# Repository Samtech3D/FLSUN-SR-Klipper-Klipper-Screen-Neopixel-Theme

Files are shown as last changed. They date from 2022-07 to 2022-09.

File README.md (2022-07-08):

If you like my Work Buy Me a Coffee! 🌹❤😍💙

Download (https://www.paypal.me/samiartmedia)

**This repository contains settings for Klipper, KlipperScreen and Neopixel for FLSUN Super Racer with necessary scripts and macros using MKS Robin Nano V3.0 motherboard.**<br /><br />

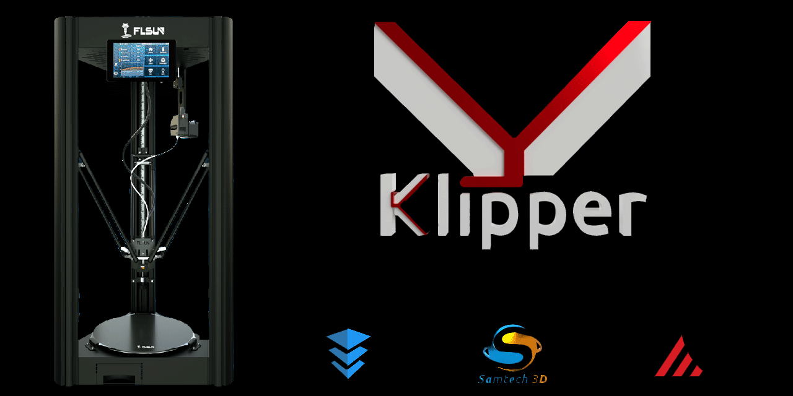
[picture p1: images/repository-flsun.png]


## References
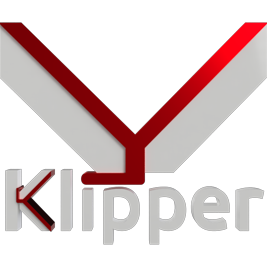
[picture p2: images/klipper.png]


- https://www.klipper3d.org/
- https://github.com/th33xitus/kiauh
- https://github.com/jordanruthe/KlipperScreen
- https://www.klipper3d.org/Pressure_Advance.html
- https://www.klipper3d.org/Resonance_Compensation.html
- https://www.klipper3d.org/Measuring_Resonances.html
- https://github.com/digitalninja-ro/klipper-neopixel

## Hardware
- The recommended hardware is a Raspberry Pi 2, Raspberry Pi 3, or Raspberry Pi 4 https://www.klipper3d.org/FAQ.html
- This installation is based on MKS Robin Nano V3.0 with TMC2209 stepper drivers and Raspberry Pi4 Touchscreen Display  "Work in Progress for other motheroards."
- Raspberry Pi 4 Touchscreen Display https://klipperscreen.readthedocs.io/en/latest/Hardware/
- ADXL 345 for input shaper test (optional) https://www.klipper3d.org/Measuring_Resonances.html

## Installation
- Prepare your OS image (I'm using Raspberry Pi OS Legacy (Buster version) to use omx-player to run my splash screen on startup). https://www.raspberrypi.com/software/ , or you can use Raspberry PI Imager
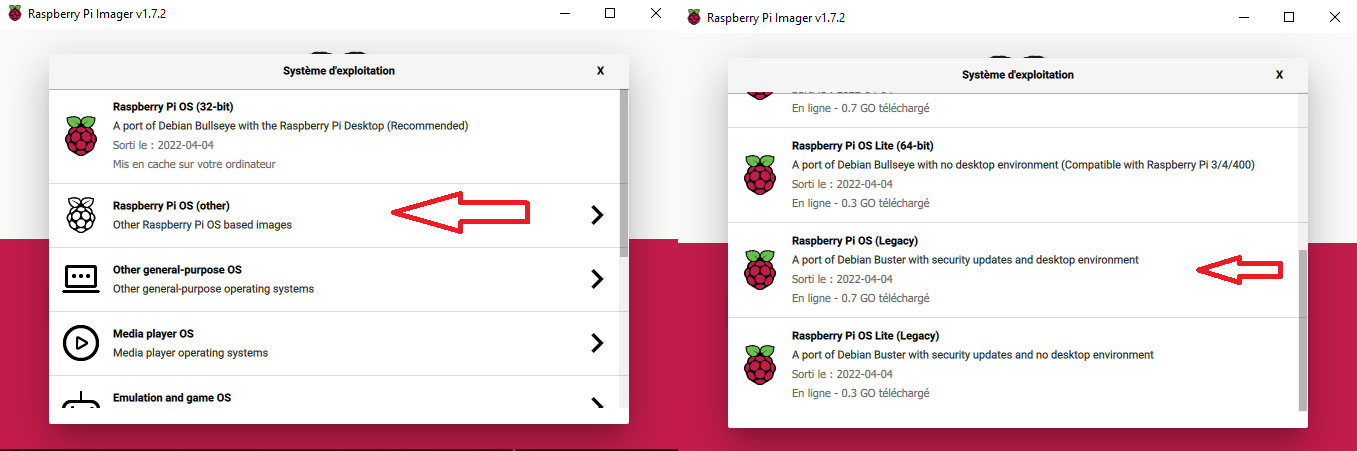
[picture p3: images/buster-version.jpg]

 
- Find the Raspberry Pi IP (you can use fing app on your phone).
- Easy way to install Klipper with Kiauh: https://github.com/th33xitus/kiauh
    - You need to install git first, on SSH run this command: `sudo apt-get install git -y`.
    - After git is installed, use the following commands in the given order to download and execute the script:

```
cd ~

git clone https://github.com/th33xitus/kiauh.git

./kiauh/kiauh.sh
```
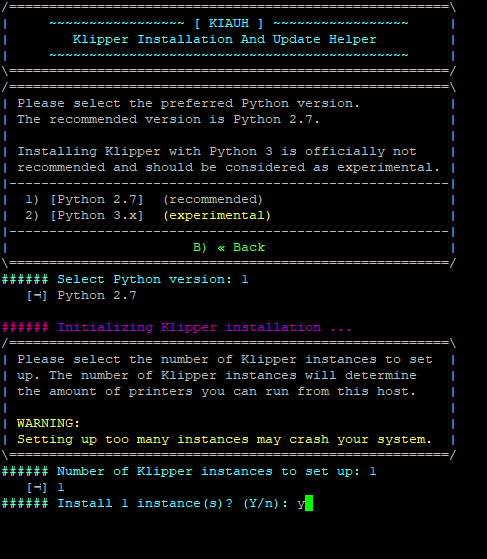
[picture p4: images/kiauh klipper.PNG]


### Install with Kiauh script in the following order:
  #### 1.Klipper
  #### 2.Moonraker
  #### 3.Fluidd or Mainsail or both using a different port for the 2nd install, example: Port 81 (I added themes for Mainsail)
  #### 4.KlipperScreen

- On your browser type your Raspberry Pi IP to open Fluidd interface then import:
    - .theme (folder)
    - printer.cfg
    - klipperScreen.conf
    - macros.cfg
    - led_progress.cfg (if you have neopixel installed) 
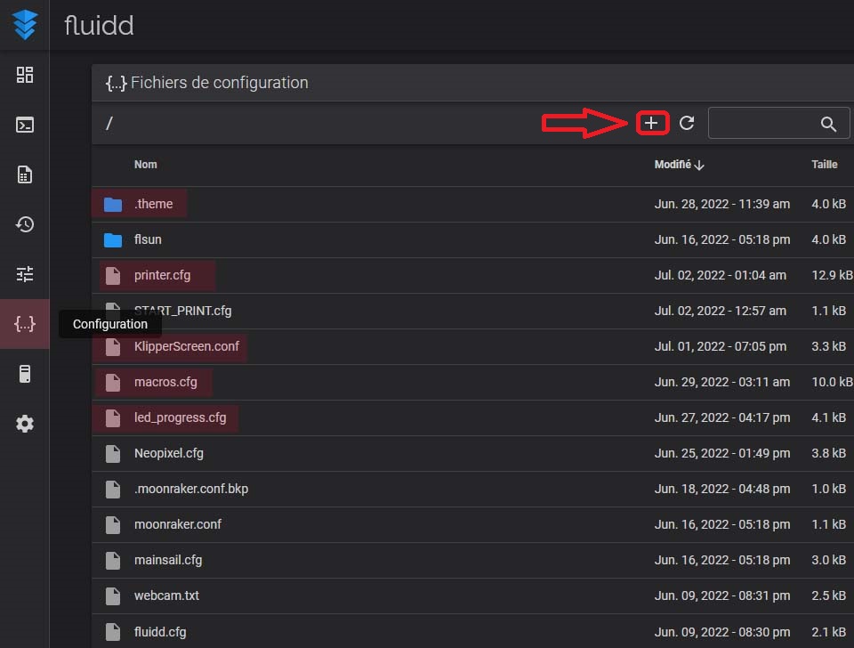
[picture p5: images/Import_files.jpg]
   

### Build firmware and flash your motherboard
- Open SSH to compile the microcontroller code, start by running these commands: 

```
cd ~/klipper/
make menuconfig
```

### [*] Enable extra low-level configuration options
### Microcontroller Architecture (STMicroelectronics STM32)  --->
  ### STMicroelectronics STM32
  ### Processor model (STM32F407)  --->
  ### Bootloader offset (48 KiB bootloader (MKS Robin Nano V3))  --->
  ### Clock Reference (8 MHz crystal)  ---> 
  ### Communication interface (USB (on PA11/PA12))  --->

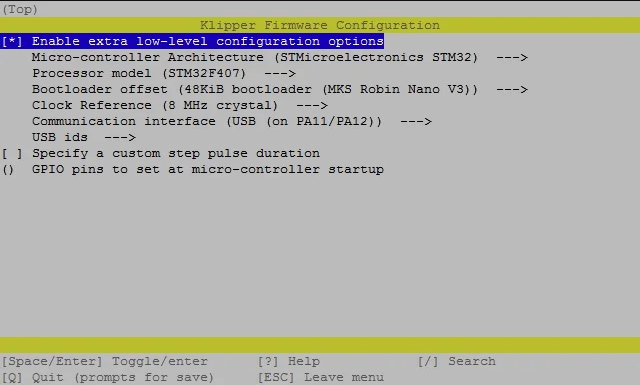
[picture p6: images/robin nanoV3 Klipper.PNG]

- Press "Q" to exit, and then "Y" to save and run make command to flashing image for your printer motherboard.

```
make
```

If you have a problem to flash your firmware enter this command:

```
make clean
git pull
make
```

- Open WinSCP App (https://winscp.net/eng/download.php), connect with your Raspberry Pi IP and navigate to:
- /home/pi/klipper/out
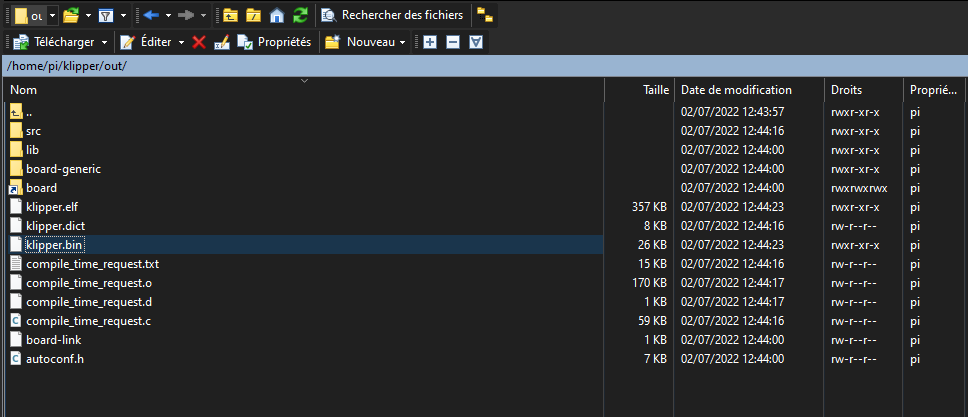
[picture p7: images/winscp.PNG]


  - Copy and paste "klipper.bin" firmware to your desktop and rename the file to "Robin_nano_v3.bin".
  - Format your microSD card (be careful, do not use the one present in the Raspberry Pi) in FAT32 with allocation unit size 4096 (max capacity 32GB) then paste "Robin_nano_v3.bin" file in the root of your  microSD card.
  - With printer off, insert the microSD card into the dedicated port on the motherboard and turn on the printer.
  - Flash procedure starts (without displaying anything on the screen) and lasts a few seconds.
  - Connect your Raspberry Pi to your printer using USB cable.
  - Comeback to your SSH session then type:

```
ls /dev/serial/by-id/*
```

It should report something similar to the following:

```
/dev/serial/by-id/usb-Klipper_stm32f407xx_4D0052000950325436303720-if00
```
   - Each printer have a unique serial
   - Copy your serial then paste it in printer.cfg


```
[mcu]
serial: /dev/serial/by-id/usb-Klipper_stm32f407xx_4D0052000950325436303720-if00#Configuration of the primary micro-controller Use ls /dev/serial/by-id/*
baud: 250000
restart_method: command
```

- If everything is correct, you can connect your Raspberry Pi with your printer.

### Calibration

## 1 - Z-Offset "You can do this with Fluidd, Mainsaill terminal or via KlipperScreen"
   - Home 
   - Make sure to connect bed level probe before to start the following command.
   - On your terminal run `PROBE_CALIBRATE` command. Printer will probe 5 times then stop at 20 mm of the bed.
   - Remove bed level probe.
   - Paper test: This involves placing a piece of plain paper between the bed and the nozzle so that the sheet of paper slightly scrapes the nozzle.
   - Use the TESTZ command to request the nozzle to move closer to the paper. For example, `TESTZ z=-1` to go down, `TESTZ z=1` to go up. It's also possible to use `TESTZ Z=+` or `TESTZ Z=-` to "bisect" the last position that is to move to a position halfway between two positions.
   - When you got the right Z-Offset, run `ACCEPT` then `SAVE_CONFIG` commands or `ABORT` command to stop the calibration procedure.
## 2 - DELTA_CALIBRATE  
  - Home.
  - Make sure to connect bed level probe before to start the following command.
  - Run `DELTA_CALIBRATE` command and wait until finish then `SAVE_CONFIG`.
## 3 - BED_MESH_CALIBRATE
  - Home
  - Make sure to connect bed level probe before to start the following command.
  - Run `BED_MESH_CALIBRATE` command and wait until finish then `SAVE_CONFIG`.
## 4 - Print 1st layer test using "1st_layer_test0.2.gcode" [ Download ] 
  - Adjust your Z-Offset while printing.
  - When it's done, run `Z_OFFSET_APPLY_PROBE` then `SAVE_CONFIG` commands to save the new Z-Offset.
  - If you still have problem with your Z-Offset, after G28 line add your Z-Offset value to your Start-Gcode, Ex:`SET_GCODE_OFFSET Z=0.35`.
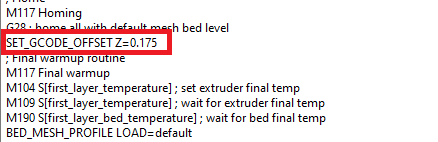
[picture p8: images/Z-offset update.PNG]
    

### Install Samtech3d Themes For Klipper Screen
  - Navigate to `/home/pi/KlipperScreen/styles` using WinSCP App then drag and drop "Samtech-red & Samtech-blue" folders.
  - In KlipperScreen Go to Configuration / Settings and scroll down to Icon Theme "Samtech-red & Samtech-blue".

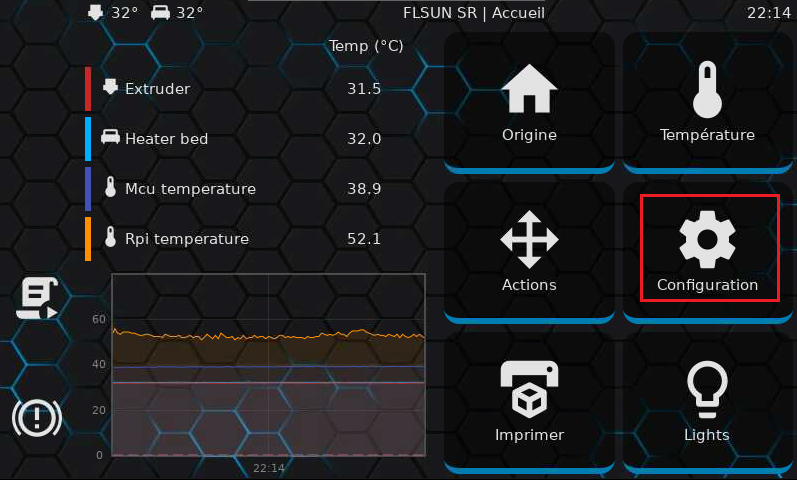
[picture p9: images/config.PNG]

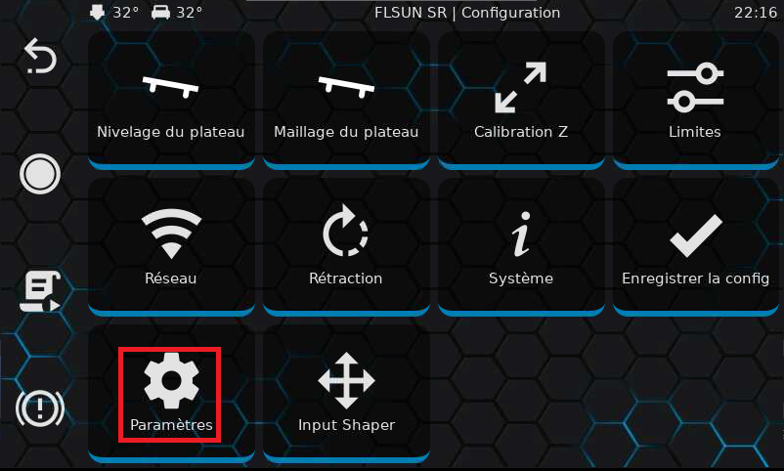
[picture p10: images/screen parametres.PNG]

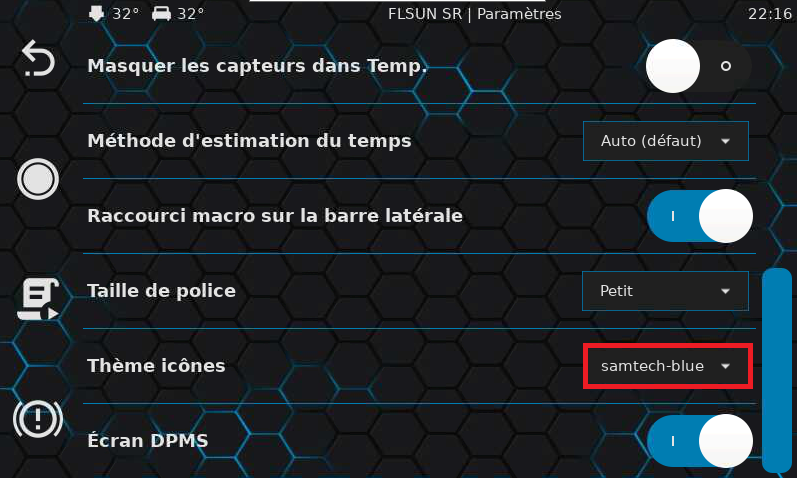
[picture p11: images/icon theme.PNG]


### Neopixel Installation

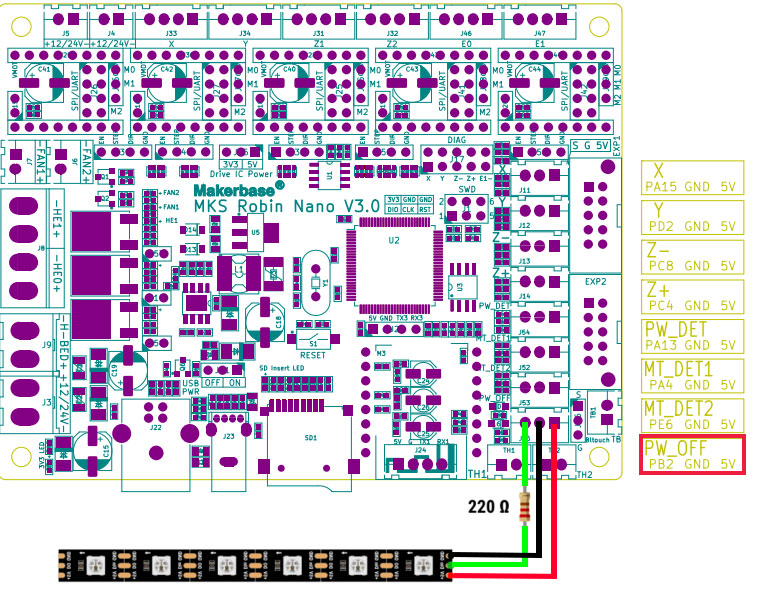
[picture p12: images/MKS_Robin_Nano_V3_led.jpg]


Or 

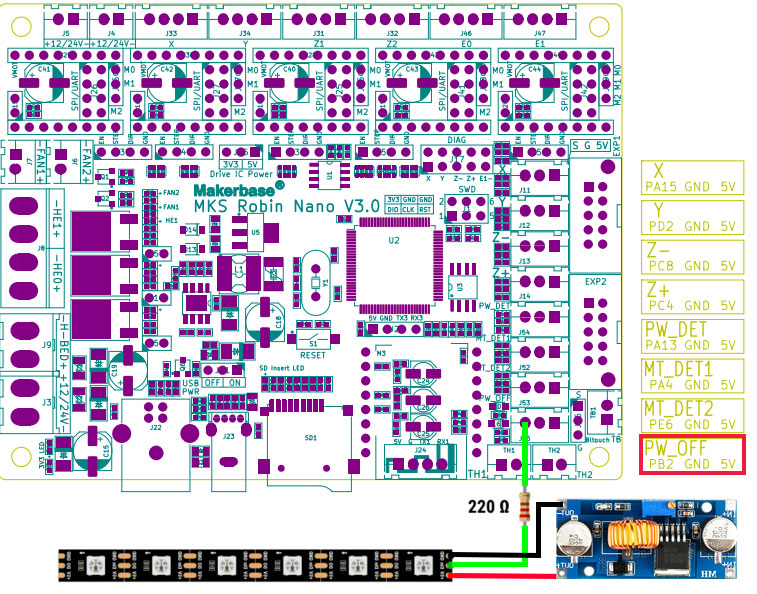
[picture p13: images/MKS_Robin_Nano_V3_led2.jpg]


  - Add `led_progress.cfg` then included in your printer.cfg `[include led_progress.cfg]`

  - Add this lines to your printer.cfg

  ```
  [neopixel neo]
  pin: PB2
  chain_count:15
  color_order: GRB
  initial_RED: 0.0
  initial_GREEN: 0.0
  initial_BLUE: 0.0
  initial_WHITE: 0.0

  ```
  - Add this lines to your KlipperScreen.conf

  ```
#####################################################
########## My Klipper Screen Neopixel  ##############
#####################################################

[menu __main Lights] #Lights
name: Lights
icon: light

[menu __main Lights Lights_On]
name: Lights On
icon: light
method: printer.gcode.script
params: {"script":"neopixel_on"}
[menu __main Lights Lights_Off]
name: Lights Off
icon: light
method: printer.gcode.script
params: {"script":"neopixel_off"}
[menu __main Lights blue]
name: blue
icon: lightB
method: printer.gcode.script
params: {"script":"blue_on"}

[menu __main Lights red]
name: red
icon: lightR
method: printer.gcode.script
params: {"script":"red_on"}
[menu __main Lights green]
name: green
icon: lightG
method: printer.gcode.script
params: {"script":"green_on"}     

[menu __main Lights extruder_temp]
name: Glow
icon: extruder
method: printer.gcode.script
params: {"script":"extrudertemp"}  
[menu __main Lights extruder_progress]
name: Progression
icon: extruder
method: printer.gcode.script
params: {"script":"extruderprogress"}  

[menu __main Lights bedtemp]
name: Glow
icon: bed
method: printer.gcode.script
params: {"script":"bedtemp"}  
[menu __main Lights bedprogress]
name: Progression
icon: bed
method: printer.gcode.script
params: {"script":"bedprogress"}  
[menu __main Lights percentprogress]
name: Progression
icon: percentage
method: printer.gcode.script
params: {"script":"percentprogress"}  
[menu __main Lights percentglow]
name: Glow
icon: percentage
method: printer.gcode.script
params: {"script":"percentglow"}  
[menu __main Lights speedprogress]
name: Progression
icon: speed+
method: printer.gcode.script
params: {"script":"speedprogress"} 
```
 - Add this lines to your macros.cfg

 ```
#############################################
######### NeoPixel By Samtech 3D#############
#############################################
[gcode_macro neopixel_on]
gcode:
          SET_LED LED=neo RED=1 GREEN=1 BLUE=1
[gcode_macro neopixel_off]
gcode:
          NEOPIXEL_DISPLAY LED="neo" TYPE=clear
          
[gcode_macro blue_on]
gcode:
          SET_LED LED=neo RED=0 GREEN=0 BLUE=1
[gcode_macro red_on]
gcode:
          SET_LED LED=neo RED=1 GREEN=0 BLUE=0   
[gcode_macro green_on]
gcode:
          SET_LED LED=neo RED=00 GREEN=1 BLUE=0  
[gcode_macro extrudertemp]
gcode:
          neopixel_display LED=neo TYPE=extruder_temp MODE=glow
[gcode_macro extruderprogress]
gcode:
          neopixel_display LED=neo TYPE=extruder_temp MODE=progress     

[gcode_macro bedtemp]
gcode:
          neopixel_display LED=neo TYPE=bed_temp MODE=glow  
[gcode_macro bedprogress]
gcode:
          neopixel_display LED=neo TYPE=bed_temp MODE=progress          
[gcode_macro percentprogress]
gcode:
          neopixel_display LED=neo TYPE=print_percent  MODE=progress        
[gcode_macro percentglow]
gcode:
          neopixel_display LED=neo TYPE=print_percent  MODE=glow   
[gcode_macro speedprogress]
gcode:
          neopixel_display LED=neo TYPE=printer_speed    MODE=progress  

[gcode_macro speedglow]
gcode:
          neopixel_display LED=neo TYPE=printer_speed    MODE=glow 

```
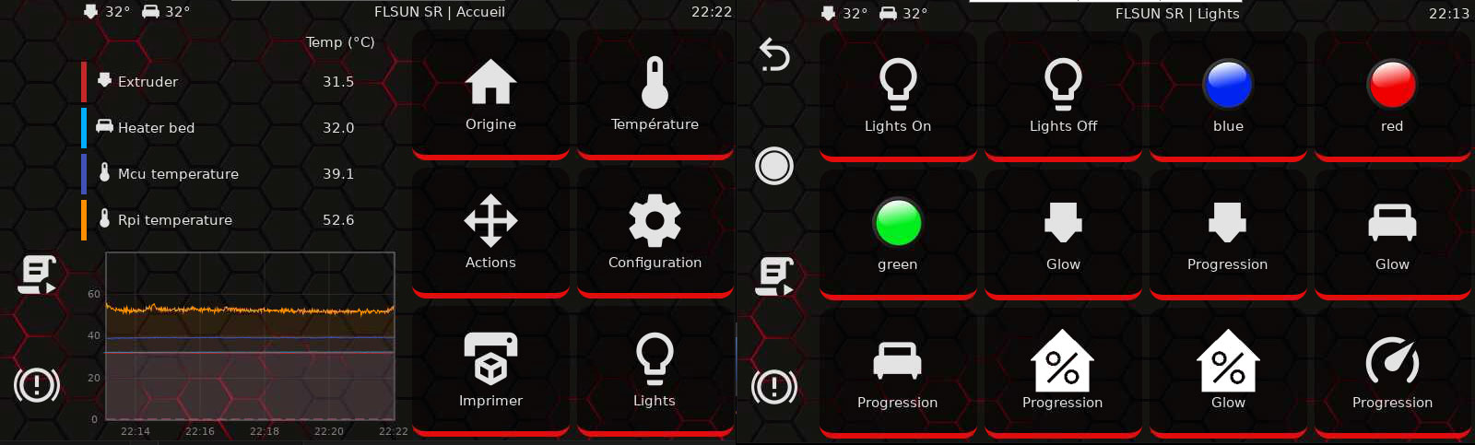
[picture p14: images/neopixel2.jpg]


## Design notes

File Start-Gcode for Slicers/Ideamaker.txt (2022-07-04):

https://github.com/Samtech3D/FLSUN-SR-Klipper-Klipper-Screen-Neopixel-Theme/blob/main/Start-Gcode%20for%20Slicers/Ideamaker.txt
M117 Initializing
G21 ; millimeter units
G90 ; absolute coordinates
M82 ; E absolute
G28 ; home axis
; Lower nozzle and move to start position
G1 Z150 F4800
G1 X-130 Y0 Z0.4 F3000
G92 E0
BED_MESH_PROFILE LOAD=default
;SET_GCODE_OFFSET Z=0.0
; Extrude about 40 mm by printing a 90 degree arc
G3 X0 Y-100 I120 Z0.5 E40 F1000
; Retract and move nozzle up
G92 E0
G1 E-0.8 F1800
G0 Z0.5
G1 E0 F300
M83

;End Gcode
M400                         ; wait for buffer to clear. avoids skipping commands
M107 T0                      ;fan off 
M104 S0                      ;set hotend temp 
M140 S0                      ;set bed temp 0  
G92 E0                       ;reset extrusion distance 
G91                          ;set relitive positioning 
G1 E-1 F300                  ;retract a bit 
G1 Z+0.5 E-5 F6000           ;raise z retract a bit more
G28 X0 Y0                    ;home x y 
G90                          ;absolute positioning
G92 E0                   ; Reset extrusion distance  
                             ; OPTIONAL LINES DELETE ; TO ENABLE 
;M18                       ; DISABLE MOTORS ALL OR USE M18 S60 =DISABLE AFTER 1 MIN S= AMOUNT OF TIME

;In post-prosses Remove T0

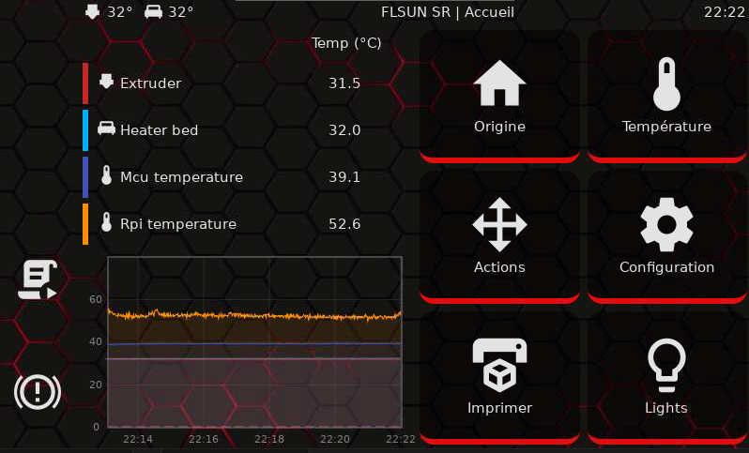
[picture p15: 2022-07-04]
images/red.PNG

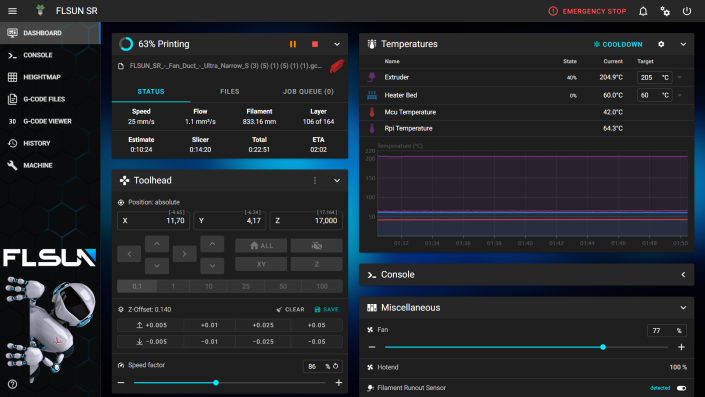
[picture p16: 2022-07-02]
images/mainsail2.png

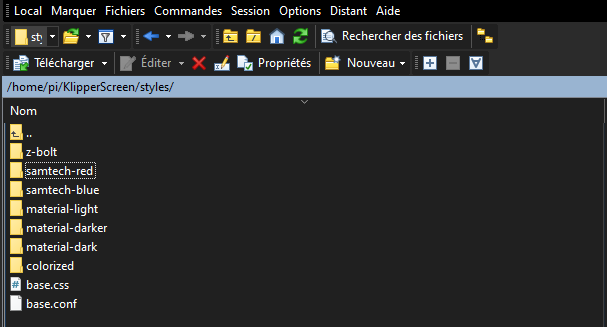
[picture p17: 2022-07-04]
images/Win SCP Theme.PNG

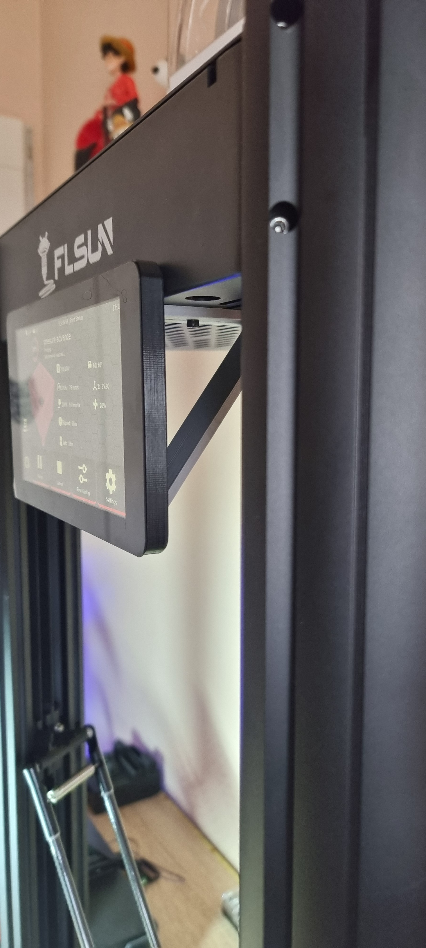
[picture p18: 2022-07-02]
images/screen_suppot2.jpg

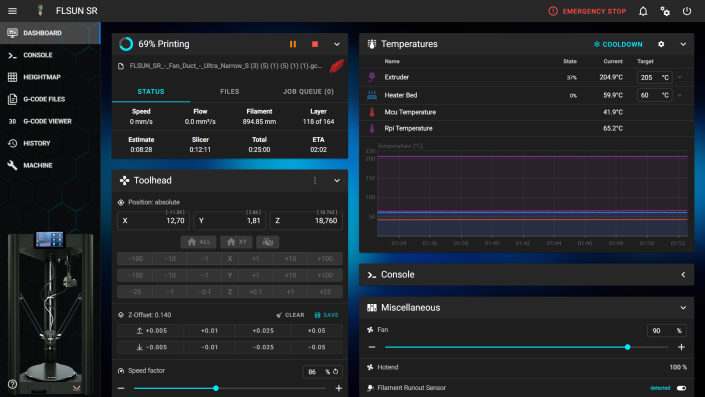
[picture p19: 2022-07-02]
images/mainsail1.png

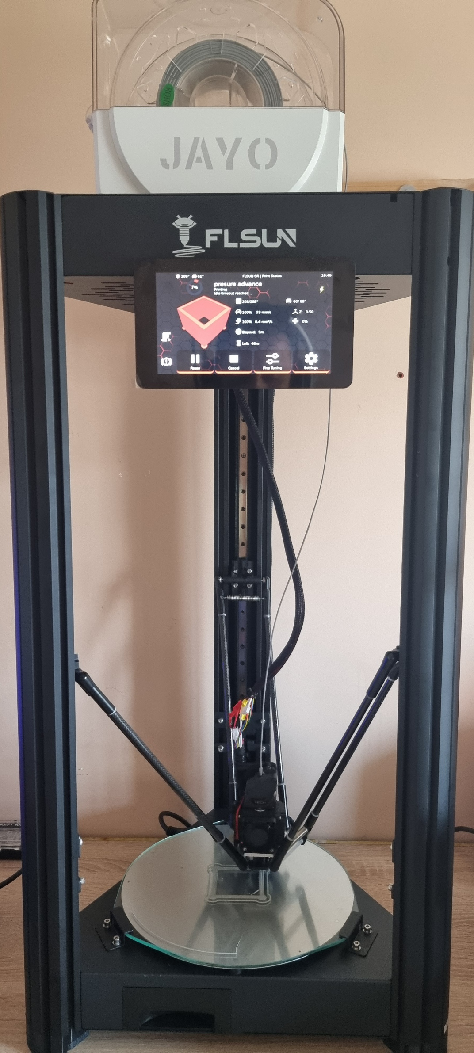
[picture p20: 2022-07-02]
images/screen_suppot1.jpg

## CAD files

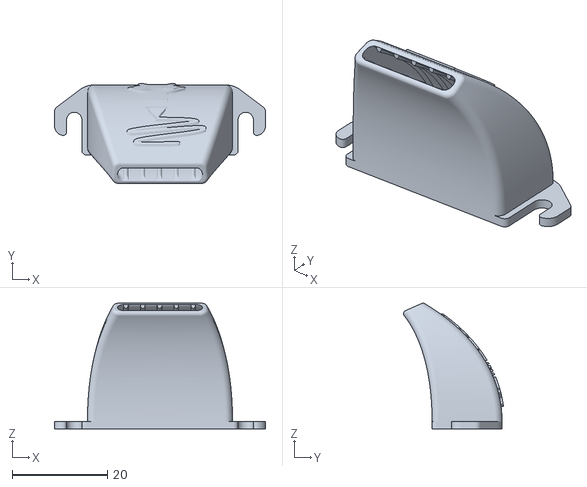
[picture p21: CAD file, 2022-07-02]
STL/FLSUN SR Fan_Duct V3 Fast Mount with logo.stl
44.3 x 21.0 x 26.4

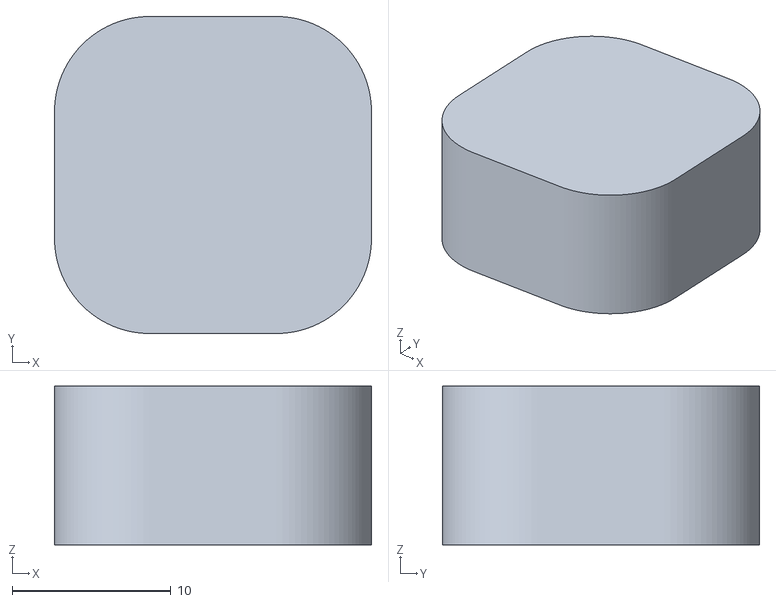
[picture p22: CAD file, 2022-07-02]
STL/piece-calibrage.stl
20.0 x 20.0 x 10.0

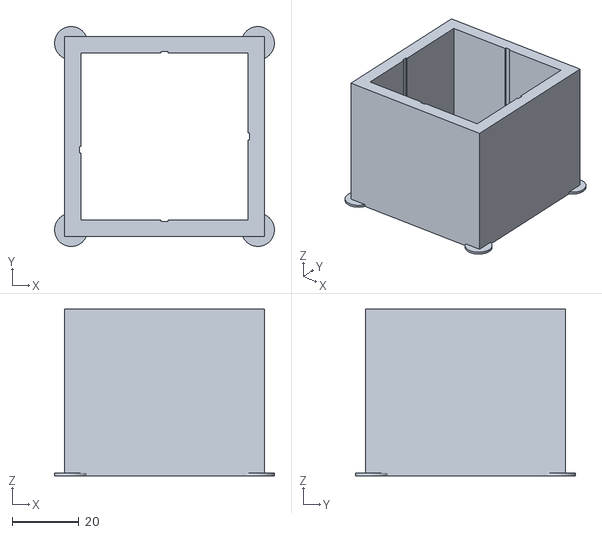
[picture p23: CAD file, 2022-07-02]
STL/square_tower(1).stl
66.0 x 65.9 x 50.0

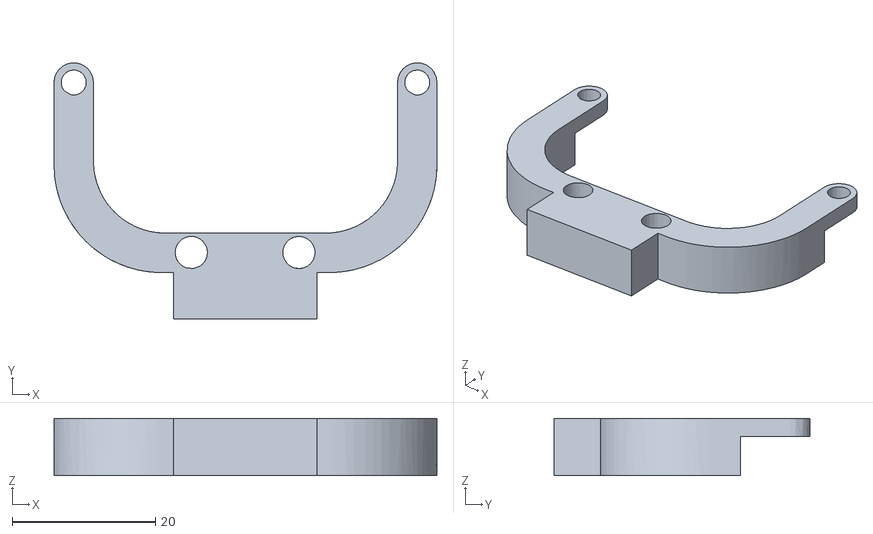
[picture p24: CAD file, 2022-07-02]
STL/FlsunSR_ADXL345_PartFanScrews_Mount.stl
53.4 x 35.8 x 8.00

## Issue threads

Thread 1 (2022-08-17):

Probleme with file name "Printer.cfg"

jstrdvid, 2022-08-17:
Hey, there is a little problem with the file name ("Printer.cfg"), you need to  rename it to "printer.cfg", replace the P with p, because Klipper create a printer.cfg and doesn't use your file cause of the first letter. (Sorry for my English, i'm French :))

Samtech3D, 2022-08-20:
Problem solved thank you

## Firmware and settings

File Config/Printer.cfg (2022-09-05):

#########################################################################
#!!!!!!!!!!!!     By Samtech 3D Flsun Super Racer     V3.0  #!!!!!!!!!!!!
################### https://github.com/Samtech3D ########################
##################### samiartmedia@yahoo.fr #############################
#########################################################################
#pin mappings for MKS Robin Nano V3
#Pross stm32f407
#Usb Enable


#  ↓   ↓   ↓   ↓   ↓   ↓   ↓   ↓   ↓   ↓   ↓   ↓   ↓   ↓   ↓   ↓   ↓   ↓ 
#########################################################################
#!!!!!!!!! DELETE SAVE CONFIG ON THE 1st RUN OF THIS CODE!!!!!!!!!!!!!!!!
#########################################################################

########################################
# Include Macros
########################################
[include fluidd.cfg]
[include macros.cfg]
[include led_progress.cfg]
#[include timelapse.cfg]
#[include ADXL345.cfg]
########################################
# MCU
########################################

[mcu]
serial: /dev/serial/by-id/usb-Klipper_stm32f407xx_4D0052000950325436303720-if00 # Configuration of the primary micro-controller Use ls /dev/serial/by-id/*
baud: 250000
restart_method: command
########################################
# ADXL345 -You need to install 2nd MCU
########################################
#[mcu rpi]
#serial: /tmp/klipper_host_mcu
#[adxl345]
#cs_pin: rpi:None
#[resonance_tester]
#accel_chip: adxl345
#probe_points:
    #0, 0, 5  # an example
    
#[input_shaper]
#shaper_type_x = zv
#shaper_freq_x = 24.2
#shaper_type_y = zv
#shaper_freq_y = 24.2        
########################################
# Temperature Sensors
########################################
[temperature_sensor Rpi mcu] 
sensor_type: temperature_host
min_temp: 10
max_temp: 100

[temperature_sensor Mcu_temp] 
sensor_type: temperature_mcu
min_temp: 0
max_temp: 100
########################################
# Printer / Steppers
########################################
[printer]
kinematics: delta
max_velocity: 300
max_accel: 3000 
max_accel_to_decel: 3200 
square_corner_velocity: 5 
max_z_accel: 3000
#max_z_velocity: 400 
delta_radius: 132 
print_radius: 132
minimum_z_position=-5 
########################################
# A (X-Stepper) Configuration
########################################
[stepper_a]
step_pin: PE3
dir_pin: PE2 
enable_pin: !PE4
microsteps: 128 
full_steps_per_rotation: 200
rotation_distance: 40
endstop_pin: ^PA15
position_endstop: 336.5 
arm_length = 315
homing_speed: 90
########################################
# B (Y-Stepper)  Configuration
########################################
[stepper_b]
step_pin: PE0
dir_pin: PB9  
enable_pin: !PE1
microsteps: 128
rotation_distance: 40
full_steps_per_rotation: 200
endstop_pin: ^PD2
position_endstop: 336.5
arm_length = 315
homing_speed: 90
########################################
# C (Z-Stepper)  Configuration
########################################
[stepper_c]
step_pin: PB5
dir_pin: PB4  
enable_pin: !PB8
microsteps: 128
rotation_distance: 40
full_steps_per_rotation: 200
endstop_pin: ^PC4
position_endstop: 336.5
arm_length = 315
homing_speed: 90
########################################
#(Extruder)  Configuration
########################################
[extruder]
step_pin: PD6
dir_pin: PD3
enable_pin: !PB3
microsteps: 16
#gear_ratio: 44:14	# THIS IS FOR BONDTECH / BMG CLONE /Stoke 
rotation_distance: 5.44 #This is for Bontech Lgx Light. MEASURE THE HOB ON THE LEVER THAT VALUE x 3.14 = ROTATION DISTANCE. FLOW IN SLICER SHOULD BE WITHIN 10 PERCENT UP OR DOWN. FILAMENT TOLERANCE AND DENSITY WILL AFFECT FLOW ACTUAL FLOW. 
full_steps_per_rotation: 200 #This is for 0.8° steppers CHANGE ME TO 400 FOR 0.9 DEGREE Steppers  ROTATION DISTANCE WILL AUTOMATICALLY BE CALIBRATED THIS APPLYS TO STEPPING AS WELL NO CHANGES REQUIRED. 
nozzle_diameter: 0.400
filament_diameter: 1.750
heater_pin: PE5
sensor_type: Generic 3950 
sensor_pin: PC1
min_temp: 0 
max_temp: 300
max_extrude_cross_section: 50 
max_extrude_only_distance: 800
pressure_advance: 0.1165  
pressure_advance_smooth_time: 0.040
instantaneous_corner_velocity: 2.5 
max_extrude_only_distance: 800.0
control = pid
pid_kp = 18.623
pid_ki = 0.554
pid_kd = 156.429
	  
########################################
# X (X-TMC)  Configuration
########################################
[tmc2209 stepper_a]
uart_pin: PD5
interpolate: false
run_current: 0.90#THIS IS RMS CURRENT NOT VREF FOR TMC. tmc spreadsheet tuned. 
driver_TBL: 2 
driver_TOFF: 2 
driver_HSTRT: 1 
driver_HEND: 3 
sense_resistor: 0.110
driver_PWM_REG: 7
driver_PWM_OFS: 36
stealthchop_threshold: 99999
########################################
# Y (Y-TMC)  Configuration
########################################
[tmc2209 stepper_b]
uart_pin: PD7
interpolate: false
run_current: 0.90 
driver_TBL: 2 
driver_TOFF: 2 
driver_HSTRT: 1 
driver_HEND: 3 
sense_resistor: 0.110
driver_PWM_REG: 7
driver_PWM_OFS: 36
stealthchop_threshold: 99999
########################################
# Z (Y-TMC)  Configuration
########################################
[tmc2209 stepper_c]
uart_pin: PD4
interpolate: false 
run_current: 0.90 
driver_TBL: 2 
driver_TOFF: 2 
driver_HSTRT: 1 
driver_HEND: 3 
sense_resistor: 0.110
driver_PWM_REG: 7
driver_PWM_OFS: 36
stealthchop_threshold: 99999
########################################
# (Extruder TMC)  Configuration
########################################
[tmc2209 extruder]
uart_pin: PD9
interpolate: false
run_current: 0.650
hold_current: 0.500
sense_resistor: 0.110
stealthchop_threshold: 999999
########################################
# Fan/Temp Configuration
########################################
[fan]
pin: PC14
max_power: 1.0
cycle_time: 0.02817 
kick_start_time: 0.0
[heater_fan heat_sink_fan] 
pin: PB0
max_power: 1.0
heater: extruder
heater_temp: 50.0
fan_speed: 1.0
max_power: 1.0
cycle_time: 0.02817 
kick_start_time: 0.0
########################################
# Bed Configuration
########################################
[heater_bed]
heater_pin: PA0
sensor_pin: PC0
sensor_type: Generic 3950
min_temp: -5
max_temp: 120 
control = pid
pid_kp = 80.041
pid_ki = 2.422
pid_kd = 300.123

[virtual_sdcard]
path: ~/gcode_files
[exclude_object]
########################################
# Delta Calibration 
########################################
[delta_calibrate]
radius: 127.5
horizontal_move_z: 25
Speed: 100
[probe] 
pin: ^!PC8 
x_offset: 0#0.599810
y_offset: 0#-1.500168
z_offset: 5
speed: 40 
samples: 3 
samples_result: average  
sample_retract_dist: 3 
samples_tolerance: 0.02 
samples_tolerance_retries: 5

[bed_mesh]  
speed: 100 
horizontal_move_z: 25
mesh_radius: 127 
mesh_origin: 0,0  
round_probe_count: 11 #11
#relative_reference_index:12
algorithm: bicubic

[force_move] #move the given stepper the given distance (in mm) at the given constant velocity (in mm/s)
enable_force_move: True

#################################
# Microstepping #################
################################## MAKE SURE TO RUN THIS FIRST THEN DELTA_CALIBRATE THEN G29/ BED_MESH_CALIBRATE. use command  endstop_phase_calibrate stepper=stepper_a  (do this for all 3 axis change the letters abc then save config) 
[endstop_phase stepper_a]
endstop_align_zero: false
[endstop_phase stepper_b]
endstop_align_zero: false
[endstop_phase stepper_c]
endstop_align_zero: false 

[firmware_retraction] # for Bondtech LGX
retract_length: 3
retract_speed: 35
unretract_speed: 30

########################################
# EXP1 / EXP2 (display) pins
########################################
[board_pins]
aliases:
    # EXP1 header
    EXP1_1=PC5,  EXP1_3=PD13, EXP1_5=PE14, EXP1_7=PD11, EXP1_9=<GND>,
    EXP1_2=PE13, EXP1_4=PC6,  EXP1_6=PE15, EXP1_8=PD10, EXP1_10=<5V>,
    # EXP2 header
    EXP2_1=PA6, EXP2_3=PE8, EXP2_5=PE11, EXP2_7=PE12,  EXP2_9=<GND>,
    EXP2_2=PA5, EXP2_4=PE10, EXP2_6=PA7, EXP2_8=<RST>, EXP2_10=<3.3v>
    # Pins EXP2_1, EXP2_6, EXP2_2 are also MISO, MOSI, SCK of bus "ssp1"

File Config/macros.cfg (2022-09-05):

#############################################################################
# Macros
#############################################################################
[pause_resume]
[gcode_arcs]
[display_status]

[gcode_macro Pid_bed_60]
gcode:
   PID_CALIBRATE HEATER=heater_bed TARGET=60
   G28
   SAVE_CONFIG 

[gcode_macro Pid_Hotend_210]
gcode:
 
   PID_CALIBRATE HEATER=extruder TARGET=210
   G28
   SAVE_CONFIG 
########################################
# Light & Neopixel
########################################    
[neopixel neo]
pin: PB2
chain_count:10
color_order: GRB
initial_RED: 0.0
initial_GREEN: 0.0
initial_BLUE: 0.0
initial_WHITE: 0.0
      

[gcode_macro led_on]
gcode:
          SET_LED LED=neo2 RED=1 GREEN=1 BLUE=1
[gcode_macro led_off]
gcode:
          NEOPIXEL_DISPLAY LED=neo2 TYPE=clear    
######### NeoPixel By Samtech 3D#############
#############################################
[gcode_macro neopixel_on]
gcode:
          SET_LED LED=neo RED=1 GREEN=1 BLUE=1
[gcode_macro neopixel_off]
gcode:
          NEOPIXEL_DISPLAY LED="neo" TYPE=clear
          
[gcode_macro blue_on]
gcode:
          SET_LED LED=neo RED=0 GREEN=0 BLUE=1
[gcode_macro red_on]
gcode:
          SET_LED LED=neo RED=1 GREEN=0 BLUE=0   
[gcode_macro green_on]
gcode:
          SET_LED LED=neo RED=00 GREEN=1 BLUE=0  
[gcode_macro extrudertemp]
gcode:
          neopixel_display LED=neo TYPE=extruder_temp MODE=glow
[gcode_macro extruderprogress]
gcode:
          neopixel_display LED=neo TYPE=extruder_temp MODE=progress     

[gcode_macro bedtemp]
gcode:
          neopixel_display LED=neo TYPE=bed_temp MODE=glow  
[gcode_macro bedprogress]
gcode:
          neopixel_display LED=neo TYPE=bed_temp MODE=progress          
[gcode_macro percentprogress]
gcode:
          neopixel_display LED=neo TYPE=print_percent  MODE=progress        
[gcode_macro percentglow]
gcode:
          neopixel_display LED=neo TYPE=print_percent  MODE=glow   
[gcode_macro speedprogress]
gcode:
          neopixel_display LED=neo TYPE=printer_speed    MODE=progress  

[gcode_macro speedglow]
gcode:
          neopixel_display LED=neo TYPE=printer_speed    MODE=glow     

#################################
# Logo marco Progressive effect
##################################
[delayed_gcode Welcome_1]
initial_duration: 0.125
gcode:
  SET_LED LED=neo GREEN=0.667 RED=0 BLUE=1 INDEX=1
  
  M300 S3000 P1
[delayed_gcode Welcome_2]
initial_duration: 0.25
gcode:
  SET_LED LED=neo GREEN=0.667 RED=0 BLUE=1 INDEX=2
  M300 S3000 P1
[delayed_gcode Welcome_3]
initial_duration: 0.375
gcode:
  SET_LED LED=neo GREEN=0.667 RED=0 BLUE=1 INDEX=3
  M300 S3000 P1
[delayed_gcode Welcome_4]
initial_duration: 1
gcode:
  SET_LED LED=neo GREEN=0.667 RED=0 BLUE=1 INDEX=4
  M300 S3000 P1
[delayed_gcode Welcome_5]
initial_duration: 0.625
gcode:
  SET_LED LED=neo GREEN=0.667 RED=0 BLUE=1 INDEX=5
  M300 S3000 P1
[delayed_gcode Welcome_6]
initial_duration: 0.75
gcode:
  SET_LED LED=neo GREEN=0.667 RED=0 BLUE=1 INDEX=6
  M300 S3000 P1
[delayed_gcode Welcome_7]
initial_duration: 0.875
gcode:
  SET_LED LED=neo GREEN=0.667 RED=0 BLUE=1 INDEX=7
  
[delayed_gcode Welcome_8]
initial_duration: 1
gcode:
  SET_LED LED=neo GREEN=0.667 RED=0 BLUE=1 INDEX=8
  
[delayed_gcode Welcome_9]
initial_duration: 1.125
gcode:
  SET_LED LED=neo GREEN=0.667 RED=0 BLUE=1 INDEX=9  
  
[delayed_gcode Welcome_10]
initial_duration: 1.25
gcode:
  SET_LED LED=neo GREEN=0.667 RED=0 BLUE=1 INDEX=10      
  

########################################
# filament_sensor 
########################################    
[filament_switch_sensor filament_sensor]
switch_pin: PA4
pause_on_runout: true
runout_gcode:
  PAUSE
  M300 S1 P1500
  M400 #Wait for current moves to finish: 
  M117 Ejecting remaining filament
  G0 E-0.4 F1500  # Quick Retract 
  G0 E-80 F1200  #eject remaining filament 
insert_gcode:
  M117 Check temps if cold set temps to print settings 1st. 
  insert_gcode: RESUME 
  
[idle_timeout] # Time in seconds (300 = 5 minutes)
timeout: 18000 #1h
gcode:
     #M300 S5 P1500
     M117 Idle timeout reached...
     #NEOPIXEL_DISPLAY LED="neo" TYPE=clear
     SET_STEPPER_ENABLE STEPPER=extruder ENABLE=0 # disable the extruder motor
     M104 S0 # set hotend to 0C
    # timeout: 100#18000 #1h
# Idle time (in seconds) to wait before running the above G-Code
# commands. The default is 600 seconds
 
   
     
[gcode_macro PAUSE]
description: Pause the actual running print
rename_existing: PAUSE_BASE
gcode:
  #M300 S1 P1500
  ##### set defaults #####
  {% set x = params.X|default(0) %}      #edit to your park position
  {% set y = params.Y|default(130) %}      #edit to your park position
  {% set z = params.Z|default(30)|float %} #edit to your park position
  {% set e = params.E|default(1) %}        #edit to your retract length
  ##### calculate save lift position #####
  {% set max_z = printer.toolhead.axis_maximum.z|float %}
  {% set act_z = printer.toolhead.position.z|float %}
  {% set lift_z = z|abs %}
  {% if act_z < (max_z - lift_z) %}
      {% set z_safe = lift_z %}
  {% else %}
      {% set z_safe = max_z - act_z %}
  {% endif %}
   ##### end of definitions #####
  PAUSE_BASE
  G91
  {% if printer.extruder.can_extrude|lower == 'true' %}
    G1 E-{e} F2100
  {% else %}
    {action_respond_info("Extruder not hot enough")}
  {% endif %}
  {% if "xyz" in printer.toolhead.homed_axes %}
    G1 Z{z_safe} 
    G90
    G1 X{x} Y{y} F6000
  {% else %}
    {action_respond_info("Printer not homed")}
  {% endif %} 

[gcode_macro CANCEL_PRINT]
description: Cancel the actual running print
rename_existing: CANCEL_PRINT_BASE
gcode:
  G28
  TURN_OFF_HEATERS
  CANCEL_PRINT_BASE
[gcode_macro RESUME]
description: Resume the actual running print
rename_existing: RESUME_BASE
gcode:
    #SET_LED LED=neo GREEN=0.667 RED=0 BLUE=1
    #M300 S1 P1500
    gcode:
    ##### set defaults #####
    {% if printer["filament_switch_sensor filament_sensor"].filament_detected == True %} 
      {% set e = params.E|default(1) %} #edit to your retract length
    #### get VELOCITY parameter if specified ####
    {% if 'VELOCITY' in params|upper %}
      {% set get_params = ('VELOCITY=' + params.VELOCITY)  %}
    {%else %}
      {% set get_params = "" %}
    {% endif %}
    ##### end of definitions #####
    G91
    {% if printer.extruder.can_extrude|lower == 'true' %}
      G1 E{e} F2100
    {% else %}
      {action_respond_info("Extruder not hot enough")}
    {% endif %}  
    RESUME_BASE {get_params}
     {% endif %} 
    
[gcode_macro ZUP]
gcode:
    SET_GCODE_OFFSET Z_ADJUST=0.025 MOVE=1

[gcode_macro ZDOWN]
gcode:
   SET_GCODE_OFFSET Z_ADJUST=-0.025 MOVE=1
########################################
# save_variables
########################################   
[save_variables]
filename: ~/savedVariables.cfg

[gcode_macro save_time]
gcode:
    {% if printer.save_variables.variables.total_time %}
        {% set print_time = printer.save_variables.variables.total_time %}
    {% else %} 
        {% set print_time = 0 %}
    {% endif %}
    {% set print_time = print_time + printer.print_stats.print_duration/3600 %}
    SAVE_VARIABLE VARIABLE=total_time VALUE={print_time}

[gcode_macro SET_GCODE_OFFSET]  
rename_existing: _SET_GCODE_OFFSET
gcode:
    {% if printer.save_variables.variables.gcode_offsets %}
        {% set offsets = printer.save_variables.variables.gcode_offsets %}
    {% else %} 
        {% set offsets = {'x': None,'y': None,'z': None} %}
    {% endif %}
    
    {% set ns = namespace(offsets={'x': offsets.x,'y': offsets.y,'z': offsets.z}) %}
    
    _SET_GCODE_OFFSET {% for p in params %}{'%s=%s '% (p, params[p])}{% endfor %}

    {%if 'X' in params %}{% set null = ns.offsets.update({'x': params.X}) %}{% endif %}
    {%if 'Y' in params %}{% set null = ns.offsets.update({'y': params.Y}) %}{% endif %}
    {%if 'Z' in params %}{% set null = ns.offsets.update({'z': params.Z}) %}{% endif %}
    {%if 'Z_ADJUST' in params %}
        {%if ns.offsets.z == None %}{% set null = ns.offsets.update({'z': 0}) %}{% endif %}
        {% set null = ns.offsets.update({'z': (ns.offsets.z | float) + (params.Z_ADJUST | float)}) %}
    {% endif %}
    SAVE_VARIABLE VARIABLE=gcode_offsets VALUE="{ns.offsets}"

[delayed_gcode LOAD_GCODE_OFFSETS]
initial_duration: 2
gcode:  
    {% if printer.save_variables.variables.gcode_offsets %}
        {% set offsets = printer.save_variables.variables.gcode_offsets %}

        _SET_GCODE_OFFSET {% for axis, offset in offsets.items() if offsets[axis] %}{ "%s=%s " % (axis, offset) }{% endfor %}

        { action_respond_info("Loaded gcode offsets from saved variables [%s]" % (offsets)) }
    {% endif %}|

[verify_heater extruder]
max_error: 500
hysteresis: 20

[gcode_macro bed_Mesh]
gcode:
  SET_GCODE_OFFSET Z=0
  G28
  delta_calibrate
  G1 X0 Y0 Z50 F4200
  G28
  save_config

[gcode_macro UNLOAD_FILAMENT] #for Direct Drive
gcode:
    G91
#    G1 E10 F300
    G1 E-80 F800
    G90

[gcode_macro LOAD_FILAMENT] 
gcode:
    G91
    G1 E10 F800
    G1 E70 F300
    G90
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

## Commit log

2022-07-02 upload main folder
    [FLSUN SR Fan_Duct V3 Fast Mount with logo.stl, FlsunSR_ADXL345_PartFanScrews_Mount.stl, Printer.cfg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]
2022-07-04 update BMG clone rotation distance
    [Printer.cfg]
2022-07-08 add neopixel wiring
2022-08-20 change horizontal_move_z: 30
    [Printer.cfg]
2022-09-05 fix update v3.0
    [Printer.cfg, macros.cfg]
